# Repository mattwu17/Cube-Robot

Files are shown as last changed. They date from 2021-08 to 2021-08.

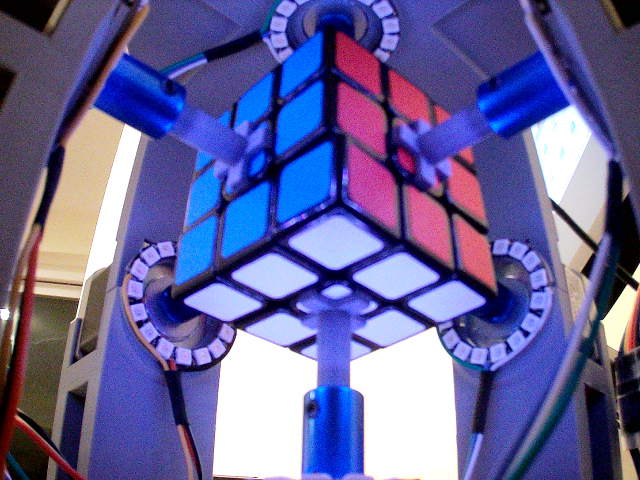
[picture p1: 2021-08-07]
Images/b_white.png

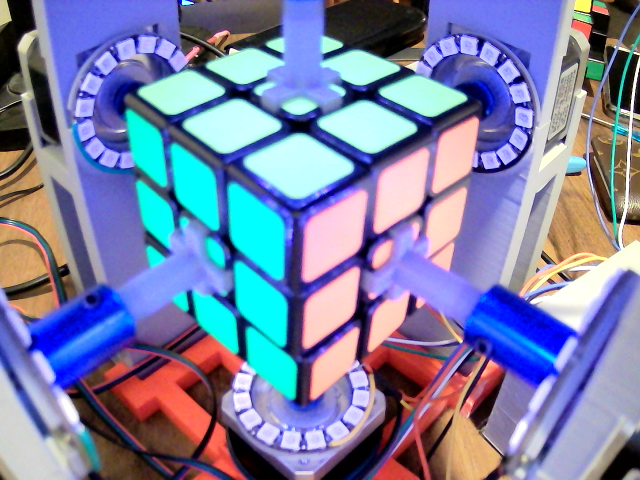
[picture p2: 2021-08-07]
Images/t_white.png

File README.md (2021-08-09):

<h1 align="center">Cube-Robot</h1>

<h2 align="center">A robot that solves Rubik's Cubes</body>

https://user-images.githubusercontent.com/69494421/128615952-5cfed673-b55f-4ff5-a4c2-c13ca85e1fac.mp4

(A random shuffle followed by an automated solve)

# Table of Contents

- [Description](#description)
- [Design](#design)
  *  [Wiring](#wiring)
  * [Required Libraries](#required-libraries)
  * [Bill of Materials](#bill-of-materials)
- [Executing program](#executing-program)
- [Acknowledgments](#acknowledgments)

## Description

Okay, a here's a more in-depth description. This cube-solving robot is made with dozens of 3D printed parts, 6 NEMA-17 stepper motors, 6 NeoPixel ring lights, 2 webcams, a Raspberry Pi, and an Arduino Uno.

The brain of the project is the Raspberry Pi, which runs the Python script which contains the commands for reading the faces of the cube and solving the cube. The Pi connects to a slave Arduino Uno via USB serial connection, sending instructions to turn the lights on/off. The Pi connects directly to drivewrs for all 6 steper motors, which each control their respective stepper motors. The Pi also connects to both webcams via USB, which are used to read the faces of the cube.

## Design

When designing the robot, there were a few specifications that I designed around:
* The robot must be able to detect all colors automatically
  * No holding the cube in front of a camera face-by-face
* The user must be able to take the cube in and out of the robot
* The user must be able to see the cube while it is being solved 

To create a program that could automatically detect all of the colors of the cube, I decided to use OpenCV in conjunction with two USB webcams. This way, the machine would be able to observe all six sides of the cube without having to rotate it (each camera sees three sides).

In order to accomodate the cube being taken both in and out of the robot, I modified a normal Rubik's Cube by carving slots in the center of each face for the rotating motor arm to latch onto. To load the cube in, the top hat can simply be removed and each arm can be pulled back slightly to allow room for the cube to slide in.

In order for users to see the cube being solved, the robot must be exposed to room lighting conditions, which are not entirely uniform. To avoid the use of a surrounding enclosure, I instead opted to add additional lighting that would ensure a consistent state for each time the robot operates.

Initial Prototype

This is the initial prototype for the robot. The prototype uses a thinner support for the top motor and slightly less supportive holders for the side motors. In the final version, the top motor holder is made thicker in order to shield the cube from room lighting conditions as much as possible. Additionally, the supports for the side motors have been modified to allow for easier storage of motor wires and mounting of lights.

## Wiring

The wiring for the robot is divided into two separate areas. The first board contains 6 stepper motor drivers, as well as connections to the 12V 10A power supply used to power the stepper motors. To make this board, I tried to solder. This was my first attempt soldering a board this intricate, and with my $20 Microcenter soldering iron I stood no chance. The second board contains a breadboard along with an Arduino Uno. After the first board, I knew if I soldered it, I would never get it to work right.


The final version of the board (above), Frustration with the soldering process (below)
Soldering is hard...

## Required Libraries

To simplify this project, I relied on the use of other libraries. Most notably, I am using the Kociemba library which contains an algorithm for solving cubes that takes the state of a scrambled cube as an imput and outputs the shortest list of moves that will solve the cube.

* Kociemba (efficient solution algorithm)
```
pip install kociemba
```
* OpenCV (camera vision)
```
pip install opencv-python
```
* Numpy (matrices used with OpenCV)
```
pip install numpy
```

## Bill of Materials

Part No. | Name | Count | Price
--- | --- | --- | ---
1 | USB Camera | 2 | $9.99 
2 | NeoPixel Ring | 6 | $4.99
3 | NEMA 17 Stepper Motor | 6 | $9.49
4 | Stepper Motor Driver | 6 | $1.33
5 | 12V 10A Power Supply | 1 | $19.86
6 | Rubik's Cube | 1 | $5.99
7 | Raspberry Pi 3 B+ | 1 | $34.99
8 | Arduino Uno | 1 | $23.00
9 | 3D Printer Filament: 1kg | 1 | $16.99
TOTAL | --- | --- | $215.67

## Executing program

The executable portion of the project lies within a Python script, cube_solver.py. The script runs through a series of smaller steps:

### Declaring constants
This script uses a significant number of constants for the cameras to detect the colors on the cube. The constants defined are the coordinates of the center of each face, as well as HSV color ranges for each color on each camera.

### Initializing the Cameras and Taking Snapshots
The script begins by creating video capture objects for both of the cameras. The Raspberry Pi then sends serial information to the Arduino, instructing it to turn specified lights on and off so that photos can be taken. In total, the cameras capture 3 pictures for analysys: one in white light for the top and bottom camera, and one in blue light for the top camera.

### Creating Masks and Analyzing Snapshots
After capturing images of all sides of the cube, the script creates masks for each color being analyzed using the input color ranges. Each color receives a binary mask where pixels within the specified range of colors are selected. After creating these masks, the script iterates along the list of coordinates that mark the centers of each color square. A conditional block detects which color is present at each coordinate and appends an identifier character for each color to a string. Once the entire cube has been identified, the script performs string manipulation to make the format compatable with the Kociemba library.

### Moving the Cube
Control of the six stepper motors is handled by the Pi. A separate file, stepper.py, contains functions to initiate and turn each motor. The main script uses these functions to iterate through the list of instructions and turn the specified amount each time. 

After the final step, the script is complete and the cube will be solved. :)

## Acknowledgments

Inspiration, code snippets, etc.
* [Kociemba Library](https://pypi.org/project/kociemba/)
* [OpenCV Tutorials](https://docs.opencv.org/master/d6/d00/tutorial_py_root.html)
* [Pi/Arduino Communications](https://roboticsbackend.com/raspberry-pi-arduino-serial-communication/)

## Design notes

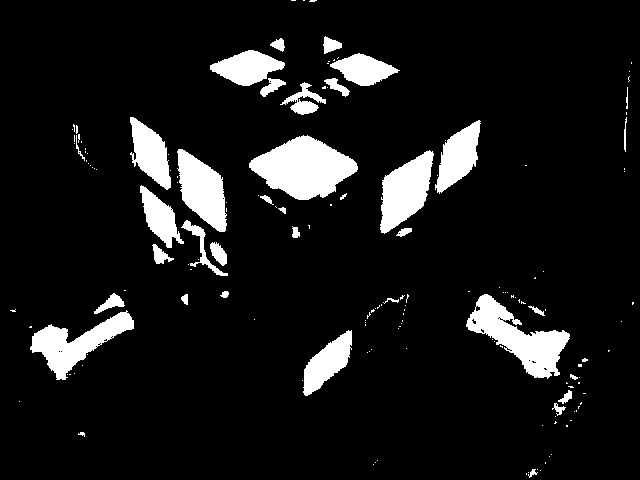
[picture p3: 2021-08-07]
Images/t_yellowmask.png

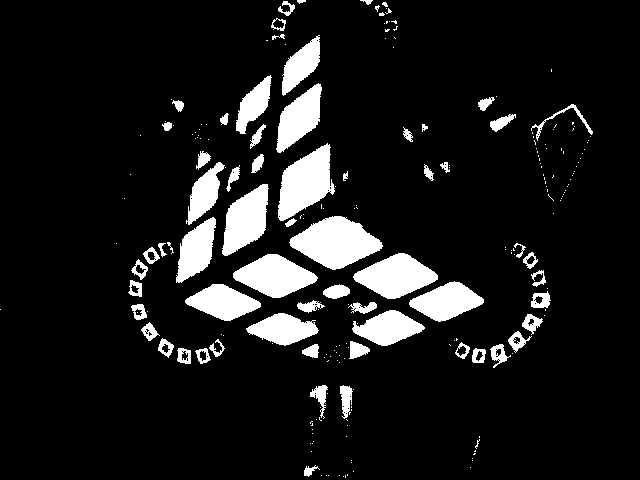
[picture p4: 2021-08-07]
Images/b_whitemask.png

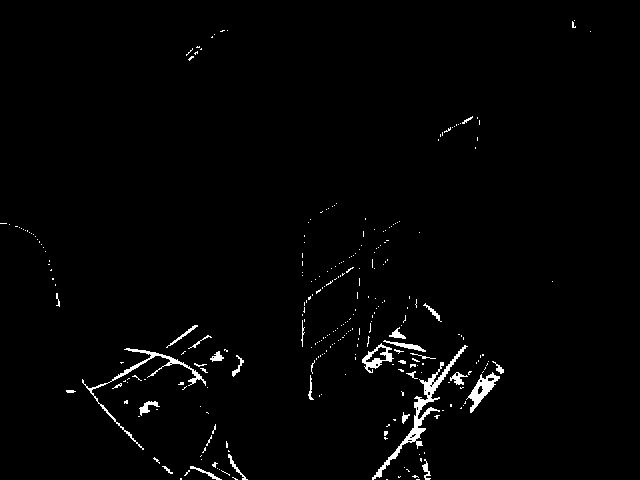
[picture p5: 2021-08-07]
Images/t_redmask.png

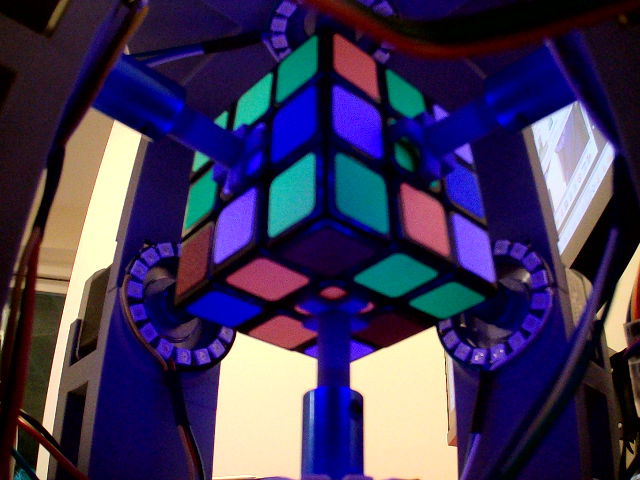
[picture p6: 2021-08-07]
Images/b_blue.png

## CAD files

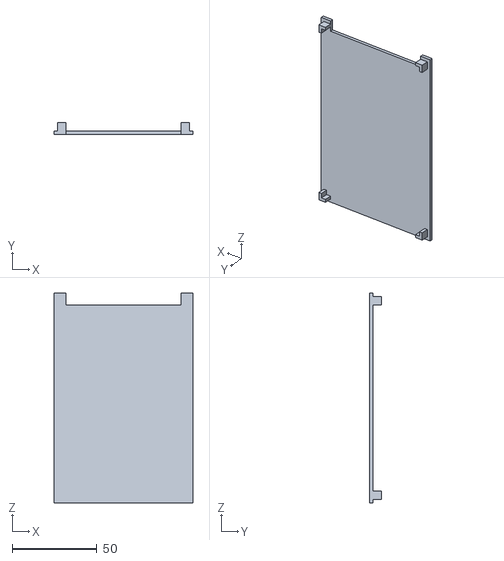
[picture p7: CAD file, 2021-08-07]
STL Files/circuitboxcover.STL
82.0 x 7.00 x 124.0

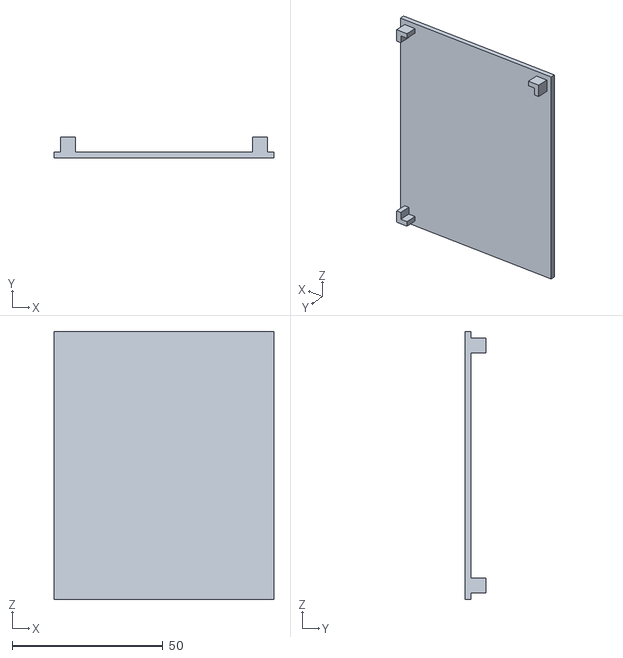
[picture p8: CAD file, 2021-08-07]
STL Files/lightboxcover.STL
73.0 x 7.00 x 89.0

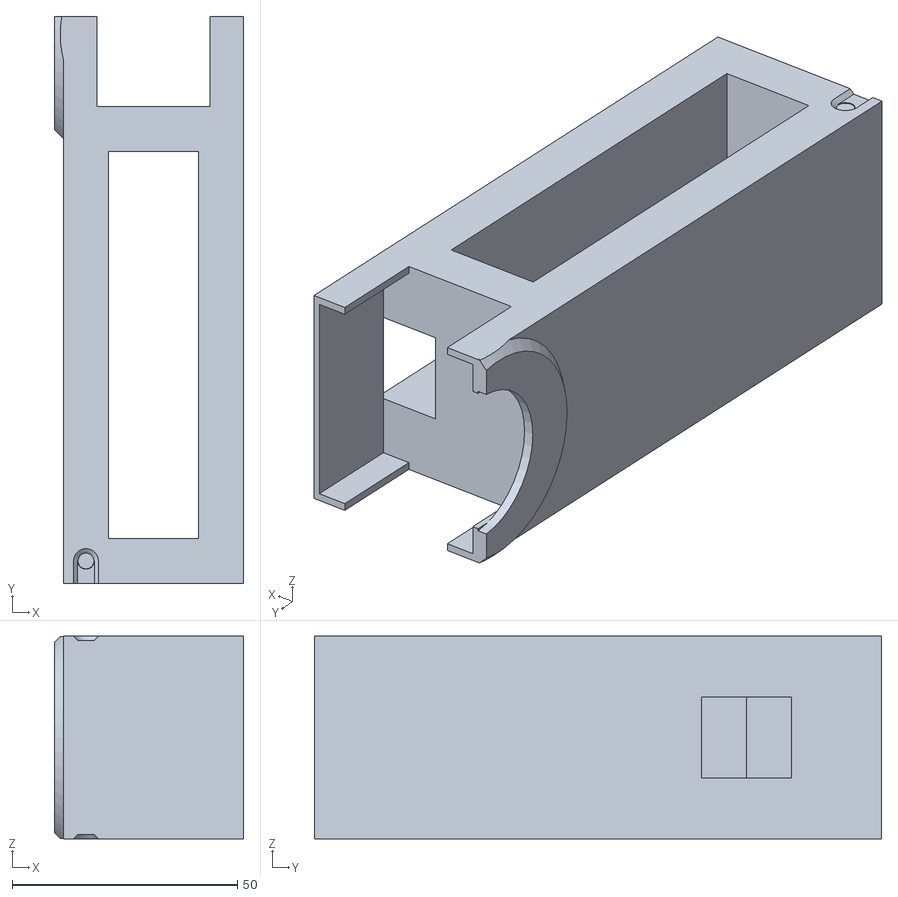
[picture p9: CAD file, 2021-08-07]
STL Files/TestHolder2.STL
42.0 x 126.0 x 45.0

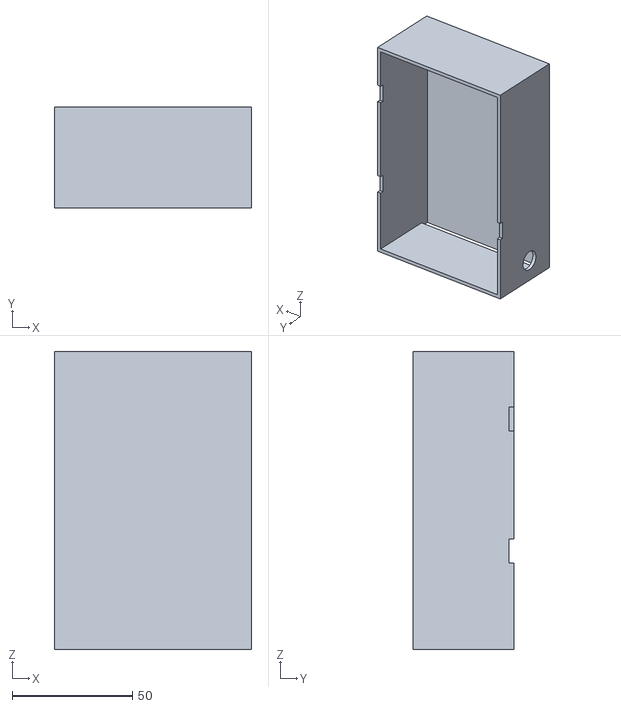
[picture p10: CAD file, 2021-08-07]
STL Files/circuitbox.STL
82.0 x 42.0 x 124.0

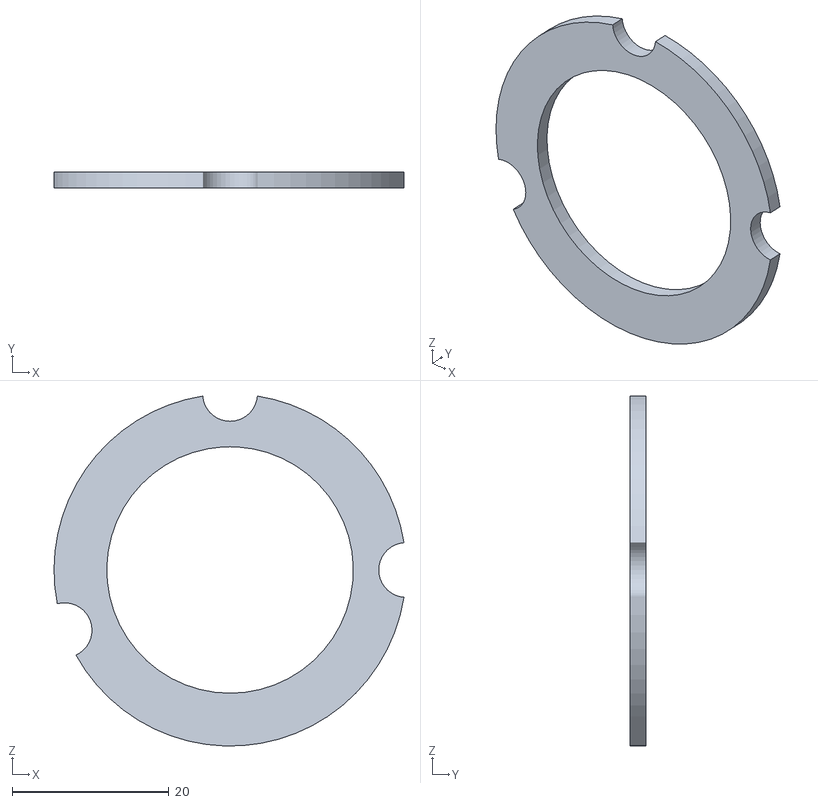
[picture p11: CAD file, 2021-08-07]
STL Files/lightplatex1.STL
44.7 x 2.00 x 44.7

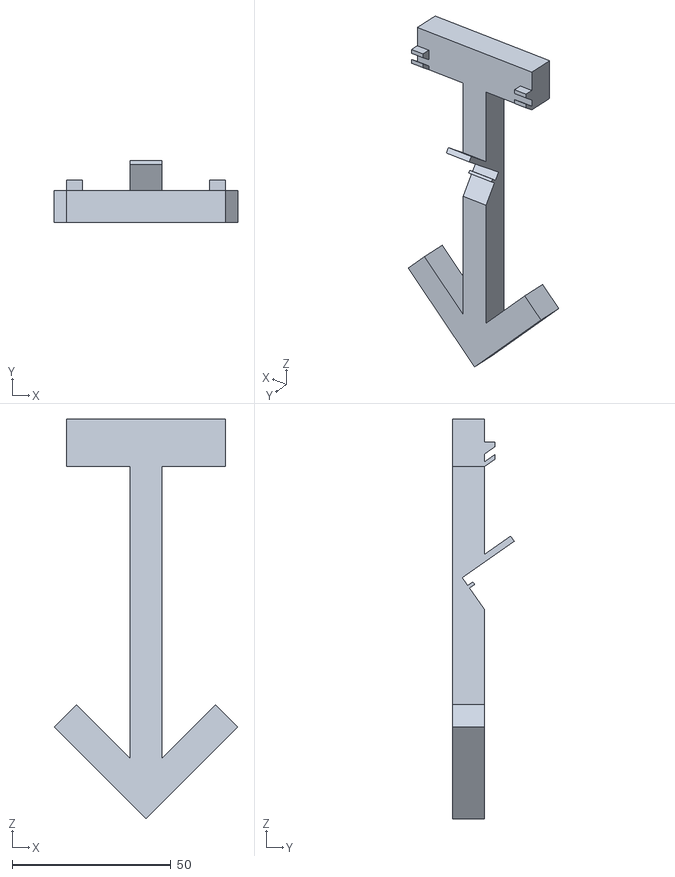
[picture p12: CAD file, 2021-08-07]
STL Files/CamHolderTest2.STL
58.0 x 19.4 x 126.1

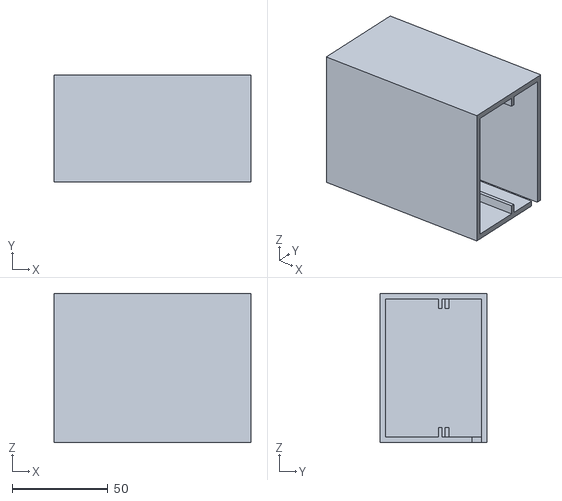
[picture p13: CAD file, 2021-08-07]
STL Files/perfshell.STL
103.0 x 56.0 x 78.0

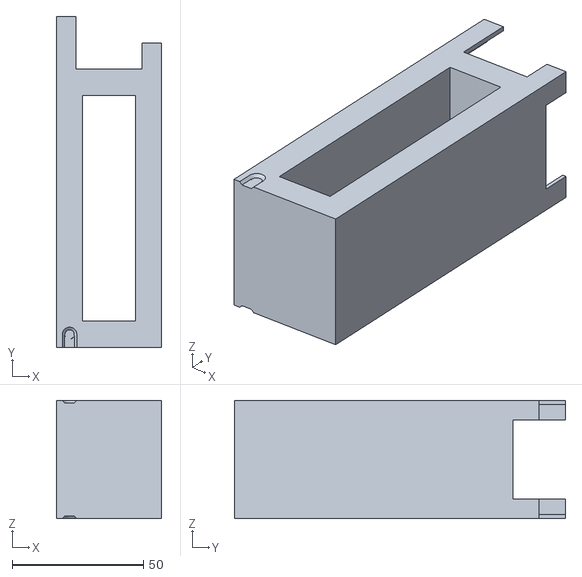
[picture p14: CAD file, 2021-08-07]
STL Files/TestHolder.STL
40.0 x 126.0 x 45.0

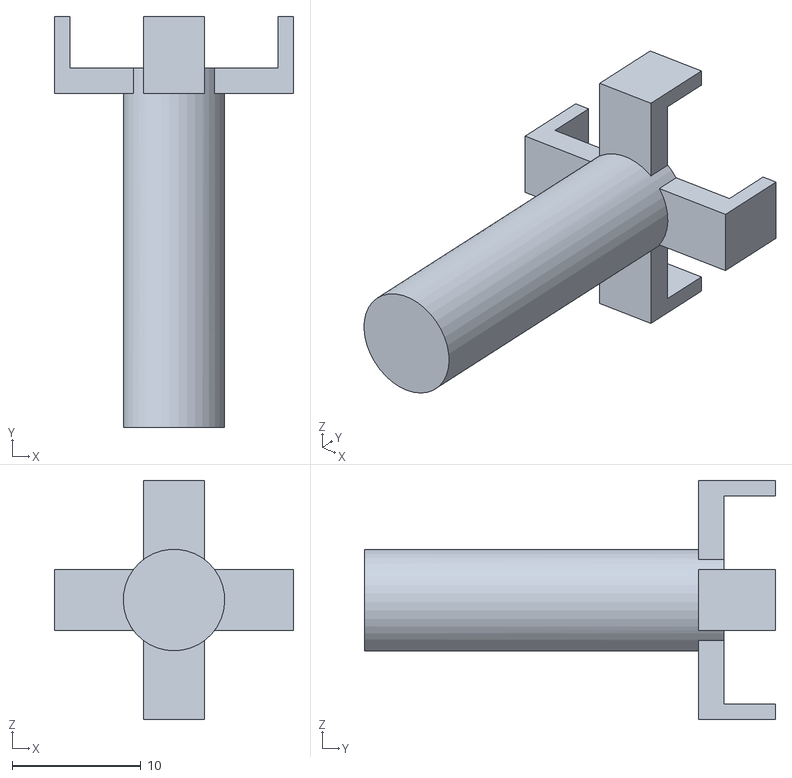
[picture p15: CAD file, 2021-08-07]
STL Files/DraftArm.STL
18.6 x 32.0 x 18.6

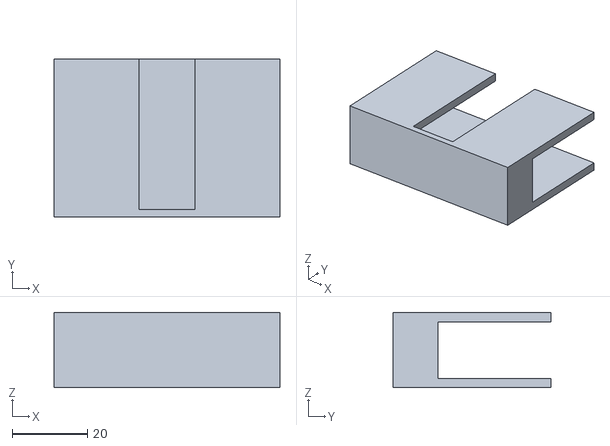
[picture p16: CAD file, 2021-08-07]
STL Files/camcover.STL
60.0 x 42.0 x 20.0

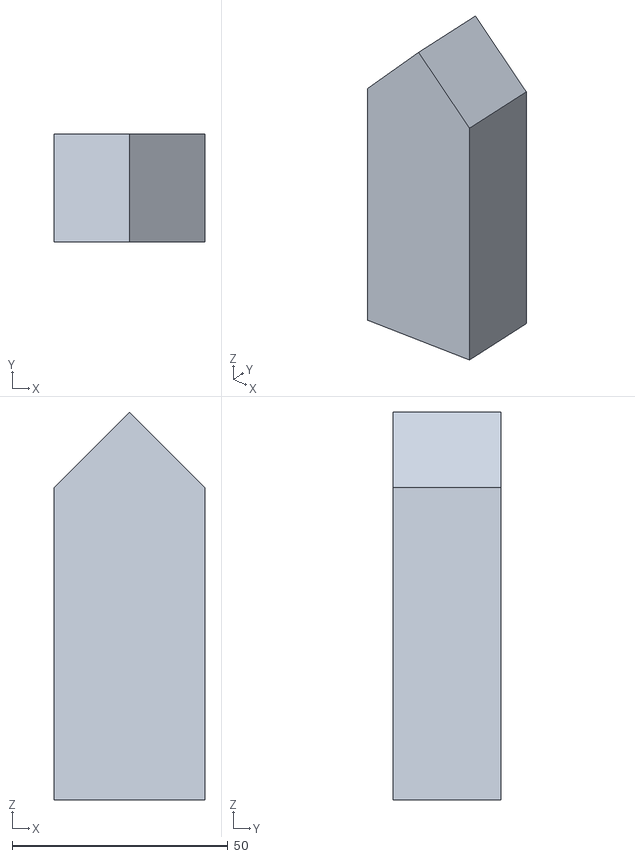
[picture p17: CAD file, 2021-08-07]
STL Files/topcamholderv2.STL
35.0 x 25.0 x 90.0

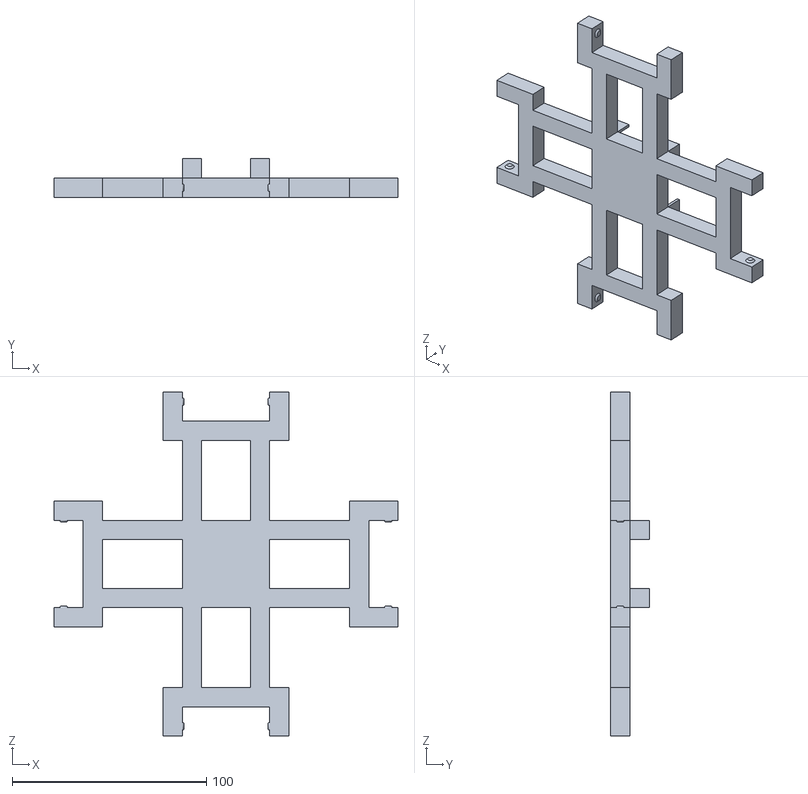
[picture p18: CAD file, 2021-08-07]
STL Files/TestBase.STL
177.0 x 20.0 x 177.0

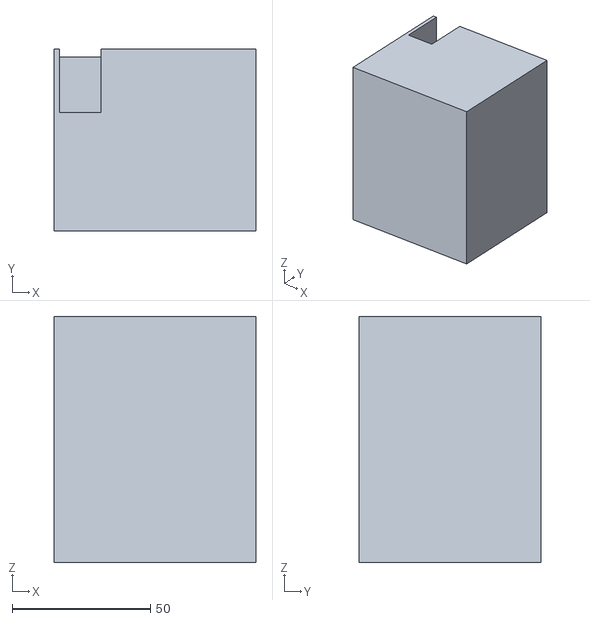
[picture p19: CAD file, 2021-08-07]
STL Files/lightbox.STL
73.0 x 66.0 x 89.0

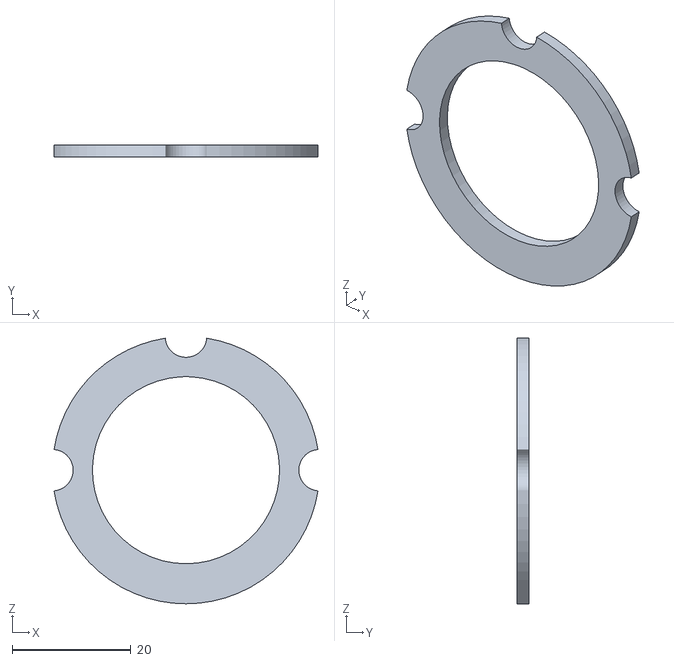
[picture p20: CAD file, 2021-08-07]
STL Files/lightplatex5.STL
44.5 x 2.00 x 44.7

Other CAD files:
STL Files/perfcap.STL
STL Files/TestHat3.STL

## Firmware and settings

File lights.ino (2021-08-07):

/*
 * Arduino slave code for Rubik's Cube Solver project
 * 
 * Code is responsible for taking in commands from Pi via serial input from USB cable and using this info to control
 * the 6 Neo Pixel ring lights that illuminate the cube
 */

#include <Adafruit_NeoPixel.h>
#ifdef __AVR__
 #include <avr/power.h> // Required for 16 MHz Adafruit Trinket
#endif

// Number of pixels on each ring - change for different hardware
#define NUMPIXELS 16 

// Pins on Arduino being used - change here if pins change
int pins[6] = {2,3,4,5,6,7};

Adafruit_NeoPixel pixels_1(NUMPIXELS, pins[0], NEO_GRB + NEO_KHZ800);
Adafruit_NeoPixel pixels_2(NUMPIXELS, pins[1], NEO_GRB + NEO_KHZ800);
Adafruit_NeoPixel pixels_3(NUMPIXELS, pins[2], NEO_GRB + NEO_KHZ800);
Adafruit_NeoPixel pixels_4(NUMPIXELS, pins[3], NEO_GRB + NEO_KHZ800);
Adafruit_NeoPixel pixels_5(NUMPIXELS, pins[4], NEO_GRB + NEO_KHZ800);
Adafruit_NeoPixel pixels_6(NUMPIXELS, pins[5], NEO_GRB + NEO_KHZ800);

#define DELAYVAL 5000 // Time (in milliseconds) to pause between pixels

void setup() {
  // begin serial connection
  Serial.begin(9600);

  // Initialization of the 6 Neo Pixel rings
  // bottom camera lights
  pixels_1.begin(); 
  pixels_2.begin();
  pixels_3.begin();

  // top camera lights
  pixels_4.begin();
  pixels_5.begin();
  pixels_6.begin();
}

void loop() {
  // detects incoming serial input
  if (Serial.available() > 0) {
    int command = Serial.read();
    
    if (command == 'B') {
      light_bottom(255,255,255);
      Serial.print("bottom lit!");
      Serial.write("\n");
    } else if (command == 'T') {
      light_top(255,255,255);
      Serial.print("top lit!");
      Serial.write("\n");
    } else if (command == 'D') {
      brightness(1);
      Serial.print("brightness: low");
      Serial.write("\n");
    } else if (command == 'L') {
      brightness(255);
      Serial.print("brightness: high");
      Serial.write("\n");
    } else if (command == 'X') {
      clear_bottom();
      Serial.print("bottom cleared");
      Serial.write("\n");
    } else if (command == 'Y') {
      clear_top();
      Serial.print("top cleared");
      Serial.write("\n");
    } else if (command == 'Z') {
      clear_all();
      Serial.print("all cleared");
      Serial.write("\n");
    } else if (command == 'M') {
      light_top(0,0,255);
      Serial.print("top lit blue!");
      Serial.write("\n");
    } else if (command == 'N') {
      light_bottom(0,0,255);
      Serial.print("bottom lit blue!");
      Serial.print("\n");
    }
  }
}

// sets the brightness of all lights to the input value
void brightness(int i) {
   pixels_1.setBrightness(i);
   pixels_2.setBrightness(i);
   pixels_3.setBrightness(i);
   pixels_4.setBrightness(i);
   pixels_5.setBrightness(i);
   pixels_6.setBrightness(i);
   
   pixels_1.show();   
   pixels_2.show();   
   pixels_3.show();
   pixels_4.show();   
   pixels_5.show();   
   pixels_6.show();
}

// lights the bottom rings
void light_bottom(int r, int g, int b) {
  for(int i=0; i<NUMPIXELS; i++) {
    // sets all light colors to white
    pixels_1.setPixelColor(i, pixels_1.Color(r, g, b));
    pixels_2.setPixelColor(i, pixels_2.Color(r, g, b));
    pixels_3.setPixelColor(i, pixels_3.Color(r, g, b));
  }

  pixels_1.show();   
  pixels_2.show();   
  pixels_3.show();
}

// lights the top rings
void light_top(int r, int g, int b) {
  for(int i=0; i<NUMPIXELS; i++) {
    // sets all light colors to white
    pixels_4.setPixelColor(i, pixels_1.Color(r, g, b));
    pixels_5.setPixelColor(i, pixels_2.Color(r, g, b));
    pixels_6.setPixelColor(i, pixels_3.Color(r, g, b));
  }

  pixels_4.show();   
  pixels_5.show();   
  pixels_6.show();
}

// clears all lights for the bottom camera
void clear_bottom() {
  pixels_1.clear(); 
  pixels_2.clear();
  pixels_3.clear();

  pixels_1.show();   
  pixels_2.show();   
  pixels_3.show();
}


void clear_top() {
  pixels_4.clear(); 
  pixels_5.clear();
  pixels_6.clear();

  pixels_4.show();   
  pixels_5.show();   
  pixels_6.show();
}

// Set all pixel colors to 'off'
void clear_all() {
  // set all pixels to have no color
  pixels_1.clear(); 
  pixels_2.clear();
  pixels_3.clear();
  pixels_4.clear();
  pixels_5.clear();
  pixels_6.clear();

  pixels_1.show();   
  pixels_2.show();   
  pixels_3.show();
  pixels_4.show();   
  pixels_5.show();   
  pixels_6.show();
}

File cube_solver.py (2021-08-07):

import cv2
import numpy as np
import time
import serial
import kociemba
import stepper

########## CONSTANTS ##########

# ALL VARIABLES PRECEEDED WITH "t_" INDICATE THEY ARE FOR TOP CAM, "b_" FOR BOTTOM CAM
t_coord_list = [(329,45),(362,67),(428,101),(247,62),(299,107),(368,128),(178,90),(231,124),(299,165),(333,241),(404,190),(457,161),(332,310),(379,256),(445,223),(327,364),(385,319),(445,262),(145,150),(197,187),(257,237),(157,215),(214,252),(261,307),(157,257),(209,314),(263,366)]
b_coord_list = [(440,304),(387,332),(356,353),(397,277),(333,293),(285,332),(332,241),(274,277),(227,307),(361,65),(412,102),(466,155),(362,113),(405,161),(466,190),(367,177),(427,220),(475,253),(203,159),(251,106),(303,63),(203,194),(258,163),(300,116),(197,256),(240,222),(296,179)]

# RANGES FOR MASKS
# orange has HSV hue value that wraps around circle, so we have 2 masks
t_lower_red = np.array([150,110,110])
t_upper_red = np.array([179,255,255])
t_lower_orange = np.array([0,20,10])
t_upper_orange = np.array([20,255,255])
t_lower_orange_2 = np.array([130,0,170])
t_upper_orange_2 = np.array([179,255,255])
t_lower_green = np.array([80,100,50])
t_upper_green = np.array([93,255,255])
t_lower_blue = np.array([95,225,225])
t_upper_blue = np.array([115,255,255])
t_lower_white = np.array([93,0,254])
t_upper_white = np.array([130,255,255])

b_lower_red = np.array([145,128,120])
b_upper_red = np.array([179,255,245])
b_lower_green = np.array([70,200,100])
b_upper_green = np.array([93,255,255])
b_lower_blue = np.array([94,160,100])
b_upper_blue = np.array([118,255,255])
b_lower_white = np.array([94,0,254])
b_upper_white = np.array([130,255,255])
b_lower_yellow = np.array([63,0,0])
b_upper_yellow = np.array([103,255,255])

########## CODE ##########

def main():
    # ser used to communicate with Arduino
    ser = serial.Serial(port='/dev/ttyACM0',baudrate = 9600,parity=serial.PARITY_NONE, stopbits=serial.STOPBITS_ONE,bytesize=serial.EIGHTBITS,timeout=1)

    # creates a cam object
    b_cam = cv2.VideoCapture(0)
    t_cam = cv2.VideoCapture(2)
    
    # try-except block across whole code
    try:
        ########## IMAGE CAPTURE ##########
        
        # "warms up" serial connection once before beginning
        ser.write(b'D')
        time.sleep(1)
        
        # gets a lit frame
        ser.write(b'D')
        ser.write(b'T')
        for i in range(50):
            _, t_lit_frame = t_cam.read()
        
        # gets a blue frame
        ser.write(b'M')
        for i in range(50):
            _, t_blue_frame = t_cam.read()
        
        # turns off the lights when they are no longer needed
        ser.write(b'Y')
        
        # gets a lit frame
        ser.write(b'B')
        for i in range(50):
            _, b_lit_frame = b_cam.read()
        
        # turns off the lights when they are no longer needed
        ser.write(b'X')
        
        ########## IMAGE PROCESSING ##########
        
        # convert all frames to HSV
        t_hsv_lit = cv2.cvtColor(t_lit_frame, cv2.COLOR_BGR2HSV)
        t_hsv_blue = cv2.cvtColor(t_blue_frame, cv2.COLOR_BGR2HSV)
        b_hsv_lit = cv2.cvtColor(b_lit_frame, cv2.COLOR_BGR2HSV)
        
        # create a new mask for every color we will detect
        t_red_mask = cv2.inRange(t_hsv_lit, t_lower_red, t_upper_red)
        t_orange_mask = cv2.inRange(t_hsv_lit, t_lower_orange, t_upper_orange)
        t_orange_mask_2 = cv2.inRange(t_hsv_lit, t_lower_orange_2, t_upper_orange_2)
        t_green_mask = cv2.inRange(t_hsv_lit, t_lower_green, t_upper_green)
        t_blue_mask = cv2.inRange(t_hsv_lit, t_lower_blue, t_upper_blue)
        t_white_mask = cv2.inRange(t_hsv_blue, t_lower_white, t_upper_white)
        b_red_mask = cv2.inRange(b_hsv_lit, b_lower_red, b_upper_red)
        b_green_mask = cv2.inRange(b_hsv_lit, b_lower_green, b_upper_green)
        b_blue_mask = cv2.inRange(b_hsv_lit, b_lower_blue, b_upper_blue)
        b_white_mask = cv2.inRange(b_hsv_lit, b_lower_white, b_upper_white)
        b_yellow_mask = cv2.inRange(b_hsv_lit, b_lower_yellow, b_upper_yellow)
        
        # writes images to file, useful for debugging
        """
        cv2.imwrite("t_redmask.png",t_red_mask)
        cv2.imwrite("t_orangemask.png",t_orange_mask)
        cv2.imwrite("t_orangemask2.png",t_orange_mask_2)
        cv2.imwrite("t_greenmask.png",t_green_mask)
        cv2.imwrite("t_bluemask.png",t_blue_mask)
        cv2.imwrite("t_whitemask.png",t_white_mask)
        cv2.imwrite("t_blue.png", t_blue_frame)
        cv2.imwrite("t_white.png", t_lit_frame)
        cv2.imwrite("b_redmask.png",b_red_mask)
        cv2.imwrite("b_greenmask.png",b_green_mask)
        cv2.imwrite("b_bluemask.png",b_blue_mask)
        cv2.imwrite("b_whitemask.png",b_white_mask)
        cv2.imwrite("b_yellowmask.png", b_yellow_mask)
        cv2.imwrite("b_white.png", b_lit_frame)
        """
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

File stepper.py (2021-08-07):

'''
This file contains functions to control the motion of the six stepper
motors used by the Rubiks Cube solver. The pins associated with each
motor are stored at matching indices of step and direction arrays.
'''

from time import sleep
import RPi.GPIO as GPIO

DELAY = 0.001
# CW / CCW are relative to the CUBE
CW = 0
CCW = 1
SPT = 50           # steps per turn, or steps per rotation / 4

DIR = [21,16,1,25,24,15] 
STEP = [20,12,7,8,23,18]

faces = dict(U = 3, R = 1, F = 5, D = 4, L = 2, B = 0)

def setup():
    # setup pins on RPi
    GPIO.setmode(GPIO.BCM)
    GPIO.setwarnings(False)
    
    for i in range(6):
        GPIO.setup(DIR[i], GPIO.OUT)
        GPIO.setup(STEP[i], GPIO.OUT)
        GPIO.output(DIR[i], CW)
    
def turn(instr):
    # gets the current pins and face of current instruction
    face_char = instr[0]
    curr_face = faces[face_char]
    curr_dir = DIR[curr_face]
    curr_step = STEP[curr_face]
    
    if "'" in instr:
        GPIO.output(curr_dir, CCW)
    else:
        GPIO.output(curr_dir, CW)
    
    if "2" in instr:
        num_turns = 2
    elif instr == "D'":
        num_turns = 3
    else:
        num_turns = 1
    
    for i in range(SPT * num_turns):
        GPIO.output(curr_step, GPIO.HIGH)
        sleep(DELAY)
        GPIO.output(curr_step, GPIO.LOW)
        sleep(DELAY)

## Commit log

2021-08-07 Initial commit
    Arduino slave code used for controlling lights
2021-08-07 Initial commit
    STL files for robot parts
    [CamHolderTest2.STL, DraftArm.STL, TestBase.STL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]
